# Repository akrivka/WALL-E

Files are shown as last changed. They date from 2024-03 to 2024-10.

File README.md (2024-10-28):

# WALL-E

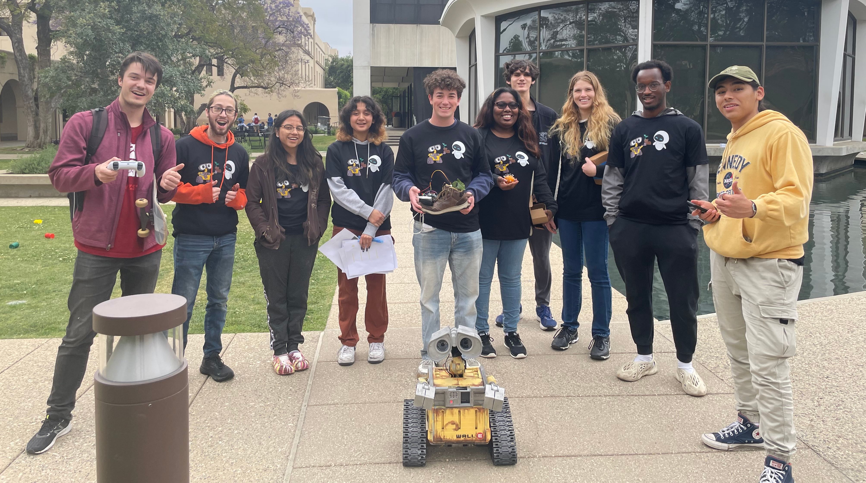
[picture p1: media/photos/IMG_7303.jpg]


For Blacker Hovse Ditch Day 2024 (Caltech tradition), we built a ~70% "real-life" size WALL-E robot, that could be **driven remotely with a PS5 controller, move his head and arms, record and transmit a video feed, speak (faintly)**, and he even had a small storage space in his body (for trash of course!).

Here's my video of him when he was at his best (he's currently sitting in a closet in Blacker to be used as a static showcase project, while I study over in Switzerland...): 

https://github.com/user-attachments/assets/6cdb80cf-8617-4d74-ad6d-1ea3f1ae313b

The model we used was https://www.thingiverse.com/thing:3703555, but we scaled it up by 5/3 which introduced a bunch of challenges. 

**! This repository was used for code-sharing and does not aim to make this project repeatable. Maybe in the future...**

## (rough) List of parts

* Rapsberry Pi 4 (Bluetooth) on Ubuntu 22.04 with ROS2 Humble installed
* PS5 controller
* [RoboClaw 2x15A Motor controller](https://www.basicmicro.com/RoboClaw-2x15A-Motor-Controller_p_10.html)
* [5202 Yellow Jacket Planetary Gear Motor](https://www.gobilda.com/5202-series-yellow-jacket-planetary-gear-motor-26-9-1-ratio-24mm-length-6mm-d-shaft-223-rpm-36mm-gearbox-3-3-5v-encoder/)
* [TowerPro MG996R servos](https://towerpro.com.tw/product/mg996r/)
* [HiLetgo PCA9685 PWM Servo Motor Driver](http://www.hiletgo.com/ProductDetail/2152091.html)
* [Small USB speaker](https://www.amazon.com/shuley-Computer-Speaker-Portable-Sound-bar/dp/B09S3G99HS/ref=sr_1_1)
* some random webcam we found
* 1x 11.1V Zeee LiPo battery (for motor), 1x 7.4V Zee LiPo battery (for servos), some random powerbank (for RPi)

## Some more photos

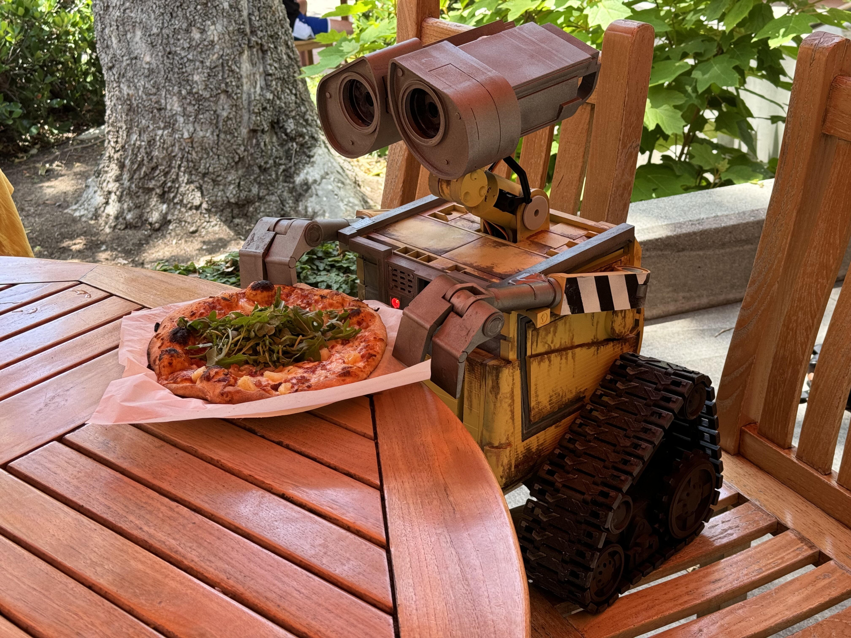
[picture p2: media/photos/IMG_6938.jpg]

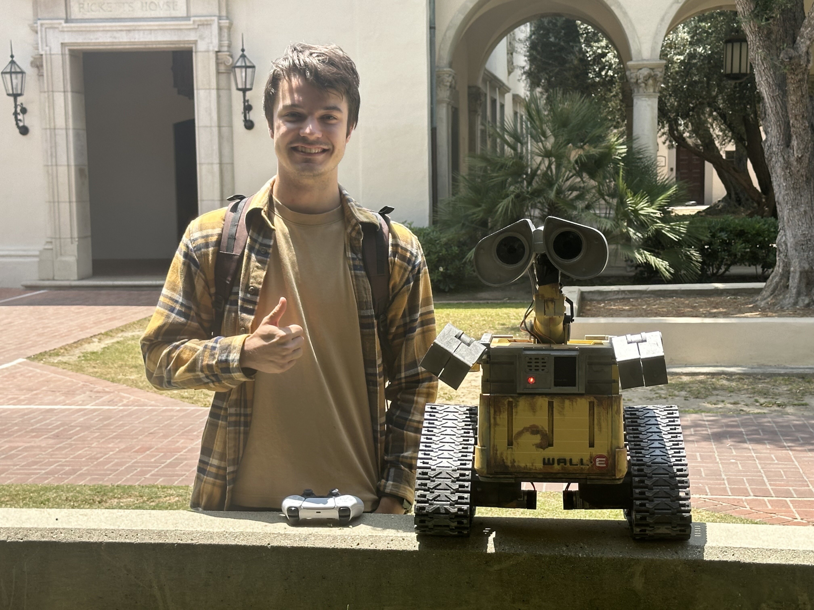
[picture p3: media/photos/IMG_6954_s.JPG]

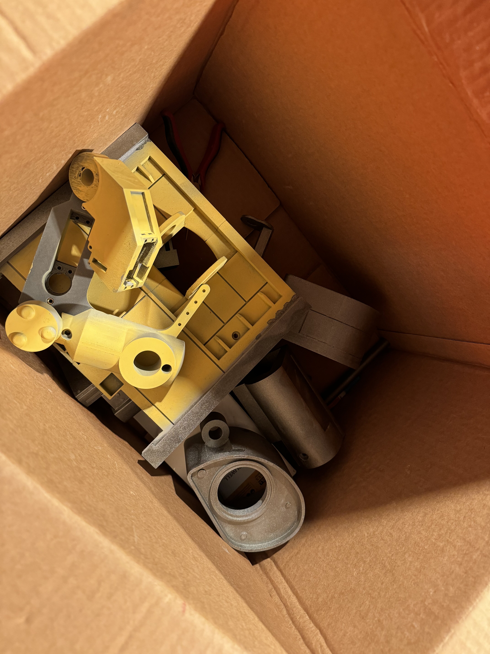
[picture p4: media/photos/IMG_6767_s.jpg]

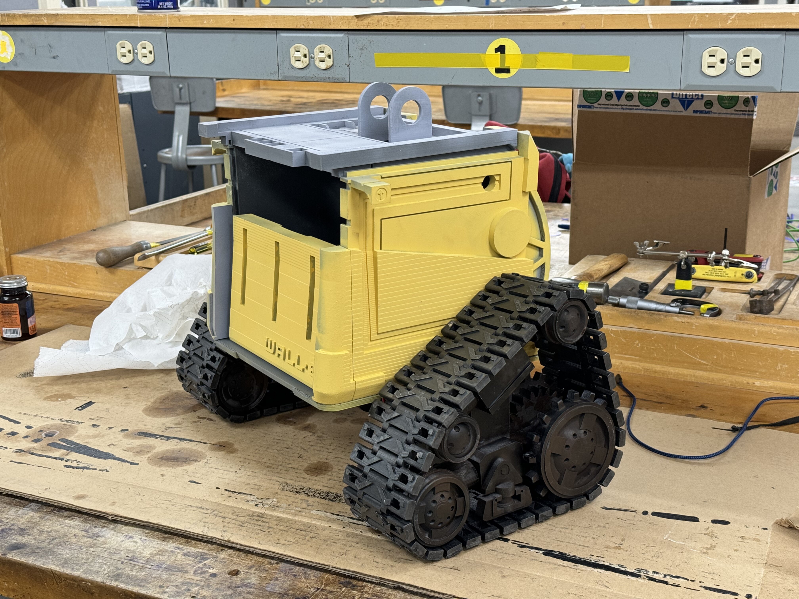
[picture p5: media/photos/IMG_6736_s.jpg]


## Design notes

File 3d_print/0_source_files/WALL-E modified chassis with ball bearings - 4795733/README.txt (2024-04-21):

WALL-E modified chassis with ball bearings by Fendermann on Thingiverse: https://www.thingiverse.com/thing:4795733

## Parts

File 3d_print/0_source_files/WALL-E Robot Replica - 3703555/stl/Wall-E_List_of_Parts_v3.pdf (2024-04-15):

3D Printed WALL-E | List of Parts
# | Name | Quantity Supports Notes

| 3D Printed Components
1 2 3 4 5 6 7 8 9 | Body body-bottom body-back body-front body-front-door body-front-pins-x2 body-left body-right body-top body-neck-servo-holder | 1 1 1 1 2 1 1 1 1 | No Yes Yes Yes No Yes Yes Yes No
10 11 12 13 14 15 16 17 18 19 20 21 22 | Arms arm-servo-bracket-left arm-servo-bracket-right arm-hinge-inner-x2 arm-hinge-outer-x2 arm-hinge-axle-x2 arm-barrel-x2 arm-barrel-end-x2 arm-piston-x2 hand-bracket-x2 hand-axle-x2 hand-finger-left-x2 hand-finger-right-x2 hand-finger-middle-x2 | 1 1 2 2 2 2 2 2 2 2 2 2 2 | No No Yes Yes No Yes No Yes Yes No No No Yes
23 24 25 26 27 28 29 30 31 | Head head-center head-axle eye-back-left eye-back-right eye-middle-left eye-middle-right eye-front-left eye-front-right eye-camera-replica | 1 1 1 1 1 1 1 1 2 | Yes No Yes Yes Yes Yes Yes Yes Yes
32 | eye-camera-mount | 0 | No | < Use this if you want
| | | | to add your own camera
| Neck
33 | neck-bottom-axle | 1 | No
34 | neck-bottom-left | 1 | Yes
35 | neck-bottom-linkage | 1 | No
36 | neck-bottom-right | 1 | Yes
37 | neck-middle-axle | 1 | No
38 | neck-top | 1 | Yes
39 | neck-round-bottom | 1 | No

40 | neck-round-top-left | 1 | Yes
41 | neck-round-top-right | 1 | Yes
42 | neck-wire-guide-left | 1 | No
43 | neck-wire-guide-right | 1 | No
44 | neck-top-linkage | 1 | No
| Wheels
45 | wheel-back-x4 | 4 | No
46 | wheel-front-x4 | 4 | No
47 | wheel-top-x8 | 8 | No
48 | wheel-top-larger-x0 | 0 | No | < Use this instead of
49 | wheel-gear-driven-x2 | 2 | No | wheel-top if you need
50 | wheel-gear-motor-x2 | 2 | No | to increase the tension
51 | wheel-axle-notched-x6 | 6 | No | of the treads.
52 | wheel-axle-back-x2 | 2 | No
53 | wheel-axle-spacer-x8 | 8 | No
54 | wheel-frame-left | 1 | No
55 | wheel-frame-right | 1 | No
56 | wheel-frame-addon-x2 | 2 | No
57 | wheel-bracket-inner-left | 1 | Yes
58 | wheel-bracket-inner-right | 1 | Yes
59 | wheel-bracket-outer-left | 1 | Yes
60 | wheel-bracket-outer-right | 1 | Yes
61 62 | Tanks Treads tread-plate-x70 tread-pin-x140 | 70 140 | No No
Total | | 310

Hardware
h1 linkage bar (paper clip) | 2
h2 M3 Bolt - 10mm length | 14
h3 M3 Bolt - 20mm length | 12
h4 M3 Bolt - 6mm length | 2
h5 M3 Nut | 26

Electronics
e1 Micro Servo Motor | 7
e2 12v Geared DC Motor ⌀37mm | 2
e3 Arduino Uno (or equivalent) | 1
e4 Arduino Motor Shield | 1
e5 12-bit PWM servo driver | 1
e6 12v Battery Pack | 1
e7 12V to 5V Buck Converter | 1
e8 Raspberry Pi | 1 | Optional
e9 USB Camera | 1
e10 Small Speaker | 1

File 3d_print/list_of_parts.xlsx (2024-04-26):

Robot – List of parts
# | Name | Quantity | Supports | Printed? | Notes
 | Body
1 | body-bottom | 1 | No
2 | body-back | 1 | Yes
3 | body-front | 1 | Yes
4 | body-front-door | 1 | Yes
5 | body-front-pins-x2 | 2 | No
6 | body-left | 1 | Yes
7 | body-right | 1 | Yes
8 | body-top | 1 | Yes
9 | body-neck-servo-holder | 1 | No
 | Arms
10 | arm-servo-bracket-left | 1 | No
11 | arm-servo-bracket-right | 1 | No
12 | arm-hinge-inner-x2 | 2 | Yes
13 | arm-hinge-outer-x2 | 2 | Yes
14 | arm-hinge-axle-x2 | 2 | No
15 | arm-barrel-x2 | 2 | Yes
16 | arm-barrel-end-x2 | 2 | No
17 | arm-piston-x2 | 2 | Yes
18 | hand-bracket-x2 | 2 | Yes
19 | hand-axle-x2 | 2 | No
20 | hand-finger-left-x2 | 2 | No
21 | hand-finger-right-x2 | 2 | No
22 | hand-finger-middle-x2 | 2 | Yes
 | Head
23 | head-center | 1 | Yes | x
24 | head-axle | 1 | No | x
25 | eye-back-left | 1 | Yes | x
26 | eye-back-right | 1 | Yes | x
27 | eye-middle-left | 1 | Yes | x | Mirror of eye-middle-right
28 | eye-middle-right | 1 | Yes | x | Altered to fit MG996R servo
29 | eye-front-left | 1 | Yes | x
30 | eye-front-right | 1 | Yes | x
31 | eye-camera-replica | 2 | Yes
32 | eye-camera-mount | 0 | No
 | Neck
33 | neck-bottom-axle | 1 | No
34 | neck-bottom-left | 1 | Yes
35 | neck-bottom-linkage | 1 | No
36 | neck-bottom-right | 1 | Yes
37 | neck-middle-axle | 1 | No
38 | neck-top | 1 | Yes
39 | neck-round-bottom | 1 | No
40 | neck-round-top-left | 1 | Yes
41 | neck-round-top-right | 1 | Yes
42 | neck-wire-guide-left | 1 | No
43 | neck-wire-guide-right | 1 | No
44 | neck-top-linkage | 1 | No
 | Wheels
45 | wheel-back-x4 | 4 | No
46 | wheel-front-x4 | 4 | No
47 | wheel-top-x8 | 8 | No
48 | wheel-top-larger-x0 | 0 | No
49 | wheel-gear-driven-x2 | 2 | No
50 | wheel-gear-motor-x2 | 2 | No
51 | wheel-axle-notched-x6 | 6 | No
52 | wheel-axle-back-x2 | 2 | No
53 | wheel-axle-spacer-x8 | 8 | No
54 | wheel-frame-left | 1 | No
55 | wheel-frame-right | 1 | No
56 | wheel-frame-addon-x2 | 2 | No
57 | wheel-bracket-inner-left | 1 | Yes
58 | wheel-bracket-inner-right | 1 | Yes
59 | wheel-bracket-outer-left | 1 | Yes
60 | wheel-bracket-outer-right | 1 | Yes
 | Tank Treads
61 | tread-plate-x70 | 70 | No
62 | tread-pin-x140 | 140 | No

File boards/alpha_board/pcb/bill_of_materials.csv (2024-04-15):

Id | Designator | Footprint | Quantity | Designation | Supplier and ref
1 | AE1 | EE110_Antenna | 1 | Antenna_Chip
2 | U8 | SOIC-14_3.9x8.7mm_P1.27mm | 1 | LM2902
3 | C17,C18 | C_0805_2012Metric_Pad1.18x1.45mm_HandSolder | 2 | 4pF
4 | R10,R12,R14 | R_0603_1608Metric_Pad0.98x0.95mm_HandSolder | 3 | 24K
5 | R15,R13,R11 | R_0603_1608Metric_Pad0.98x0.95mm_HandSolder | 3 | 36K
6 | D10,D11 | D_1206_3216Metric_Pad1.42x1.75mm_HandSolder | 2 | D_Small_Filled
7 | C1,C3,C2 | CP_EIA-1608-08_AVX-J_Pad1.25x1.05mm_HandSolder | 3 | 10uF
8 | C28 | C_0603_1608Metric_Pad1.08x0.95mm_HandSolder | 1 | 10nF
9 | C12,C21,C16,C14 | CP_EIA-1608-08_AVX-J_Pad1.25x1.05mm_HandSolder | 4 | 4.7uF
10 | ,, |  | 3
11 | C23,C26 | C_0603_1608Metric_Pad1.08x0.95mm_HandSolder | 2 | 10uF
12 | U9 | QFN-24-1EP_3x3mm_P0.4mm_EP1.75x1.6mm | 1 | MPU-9250
13 | U6 | SOIC-20W_7.5x15.4mm_P1.27mm | 1 | 74LVC245
14 | D7,D6,D4,D2,D5,D13,D12,D3 | D_0603_1608Metric_Pad1.05x0.95mm_HandSolder | 8 | D_Small_Filled
15 | C19 | C_0805_2012Metric_Pad1.18x1.45mm_HandSolder | 1 | 1pF
16 | LS1 | SPKR_CVS-1508 | 1 | Speaker
17 | C30,C27,C32,C29,C31 | C_0603_1608Metric_Pad1.08x0.95mm_HandSolder | 5 | 0.1uF
18 | D1 | LED_D3.0mm | 1 | LED
19 | C9,C7 | CP_EIA-1608-08_AVX-J_Pad1.25x1.05mm_HandSolder | 2 | 22uF
20 | J3 | 4x4_Keypad | 1 | ~
21 | C15 | C_0805_2012Metric_Pad1.18x1.45mm_HandSolder | 1 | 1.8pF
22 | RV2 | Potentiometer_Bourns_3296P_Horizontal | 1 | 1k
23 | C4,C11,C8,C5,C10,C6 | CP_EIA-1608-08_AVX-J_Pad1.25x1.05mm_HandSolder | 6 | 100nF
24 | J2 | CON10_2X5_DUK_FTSH_SAI | 1 | JTAG
25 | X1 | Crystal_SMD_2016-4Pin_2.0x1.6mm | 1 | 48MHz
26 | R8,R4,R7 | R_0603_1608Metric_Pad0.98x0.95mm_HandSolder | 3 | 200
27 | L5,L3 | L_0805_2012Metric_Pad1.15x1.40mm_HandSolder | 2 | 3.3nH
28 | L2 | L_0603_1608Metric_Pad1.05x0.95mm_HandSolder | 1 | 6.8uH
29 | RV3,RV1 | Potentiometer_Bourns_3296P_Horizontal | 2 | 10k
30 | J6 | JST_XH_S4B-XH-A-1_1x04_P2.50mm_Horizontal | 1 | SERVO2
31 | L4 | L_0805_2012Metric_Pad1.15x1.40mm_HandSolder | 1 | 2nH
32 | U2,U1 | TO-263-3_TabPin2 | 2 | LM1086
33 | SW2 | SW_SPST_TL3342 | 1 | TEST_BUTTON
34 | C24 | C_0603_1608Metric_Pad1.08x0.95mm_HandSolder | 1 | 250uF
35 | U7 | DIP-8_W7.62mm | 1 | LM386
36 | TP1 | TestPoint_THTPad_2.0x2.0mm_Drill1.0mm | 1 | DIO22
37 | TP2 | TestPoint_THTPad_2.0x2.0mm_Drill1.0mm | 1 | DIO23
38 | J5 | JST_XH_S4B-XH-A-1_1x04_P2.50mm_Horizontal | 1 | SERVO1
39 | TP3 | TestPoint_THTPad_2.0x2.0mm_Drill1.0mm | 1 | DIO24
40 | R3,R2 | R_0603_1608Metric_Pad0.98x0.95mm_HandSolder | 2 | 121
41 | SW1 | SW_SPST_TL3342 | 1 | RESET
42 | DS1 | WINSTAR-WH1604A | 1 | LCD-20X4B
43 | TP5 | TestPoint_THTPad_2.0x2.0mm_Drill1.0mm | 1 | GND
44 | C25 | C_0603_1608Metric_Pad1.08x0.95mm_HandSolder | 1 | 0.05uF
45 | TP4 | TestPoint_THTPad_2.0x2.0mm_Drill1.0mm | 1 | +3.3V
46 | U4 | RGZ0048A_NV | 1 | CC2652
47 | R6 | R_0603_1608Metric_Pad0.98x0.95mm_HandSolder | 1 | 183
48 | X2 | Crystal_SMD_3215-2Pin_3.2x1.5mm | 1 | 32.768KHz
49 | C22 | C_0603_1608Metric_Pad1.08x0.95mm_HandSolder | 1 | 1uF
50 | U5 | SOIC-16_3.9x9.9mm_P1.27mm | 1 | 74LS138
51 | D8 | LED_0603_1608Metric_Pad1.05x0.95mm_HandSolder | 1 | TEST_GREEN
52 | D9 | LED_0603_1608Metric_Pad1.05x0.95mm_HandSolder | 1 | TEST_BLUE
53 | R1 | R_0603_1608Metric_Pad0.98x0.95mm_HandSolder | 1 | 100
54 | R9 | R_0603_1608Metric_Pad0.98x0.95mm_HandSolder | 1 | 10
55 | C20,C13 | C_0805_2012Metric_Pad1.18x1.45mm_HandSolder | 2 | 1.3pF
56 | J4 | microSD_HC_Hirose_DM3D-SF | 1 | Micro_SD_Card
57 | R5 | R_0603_1608Metric_Pad0.98x0.95mm_HandSolder | 1 | 363
58 | R16 | R_0603_1608Metric_Pad0.98x0.95mm_HandSolder | 1 | 4.7k
59 | J1 | My_Power_Connector | 1 | power
60 | L1 | L_7.3x7.3_H3.5 | 1 | BLM18HE152SN1
61 | U3 | SOT-23-5 | 1 | LM372x
62 | B1 | 1049P_KEY | 1 | 1049P

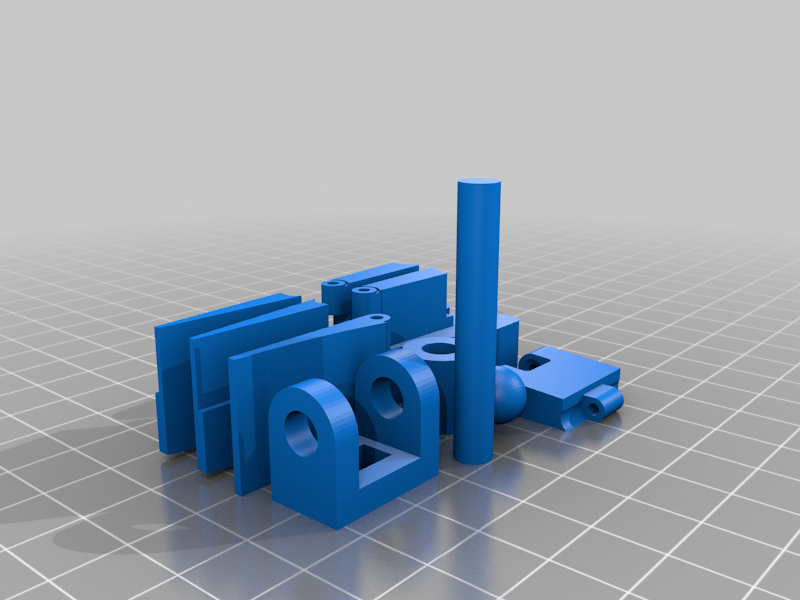
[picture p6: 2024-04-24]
3d_print/0_source_files/Wall-e realistic hand for WALL-E Robot Replica by chillibasket - 5391045/images/Wall-e_hand_parts.png

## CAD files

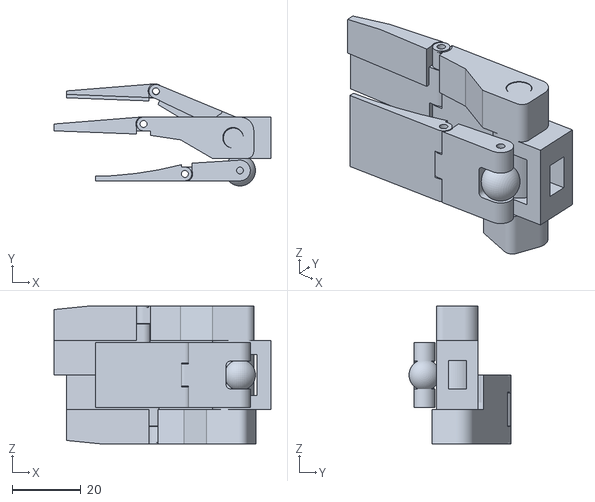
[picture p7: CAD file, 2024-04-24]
3d_print/0_source_files/Wall-e realistic hand for WALL-E Robot Replica by chillibasket - 5391045/files/Wall-e_hand_assembled.stl
63.0 x 29.6 x 40.0

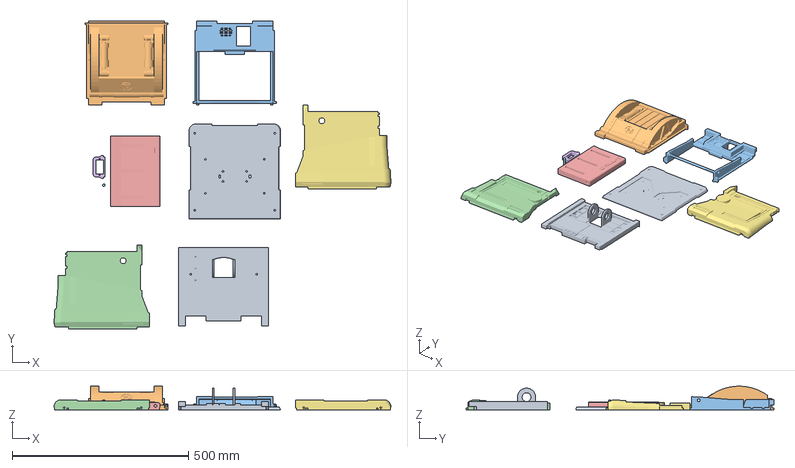
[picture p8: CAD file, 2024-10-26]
3d_print/0.1_source_files/WALL-E Robot Replica - 3703555/stl/body-back.3mf
956.4 x 873.5 x 67.2 mm
body-bottom.stl
body-back.stl
body-front.stl
body-left.stl
body-front-door.stl
body-neck-servo-holder.stl
body-right.stl
body-front-pins-x2.stl
body-top.stl

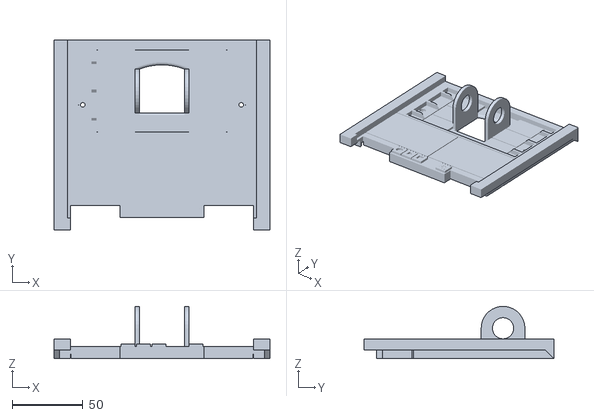
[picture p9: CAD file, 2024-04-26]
3d_print/0_source_files/Accurate Recording Buttons - 5223648/files/New_Wall-e_Top.stl
153.0 x 134.4 x 37.0

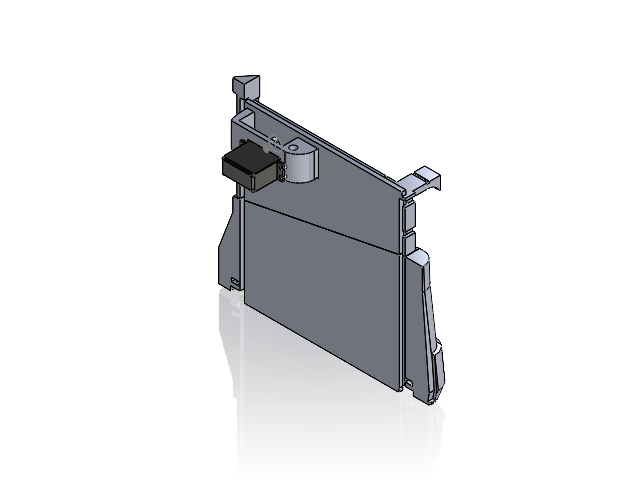
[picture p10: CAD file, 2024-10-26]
3d_print/1_cad/assemblies/body-arm.SLDASM
arm-servo-bracket-left
MG996R
body-left

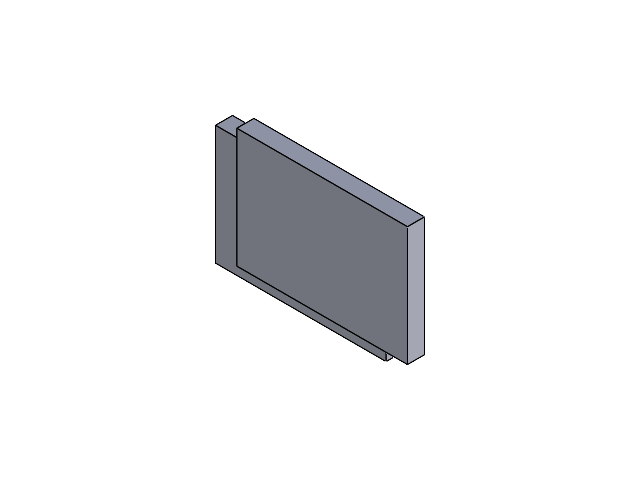
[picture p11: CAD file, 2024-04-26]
boards/alpha_board/enclosure/1_cad/assemblies/alpha_board_enclosure.SLDASM
alpha_board_enclosure_bottom
alpha_board_enclosure_top

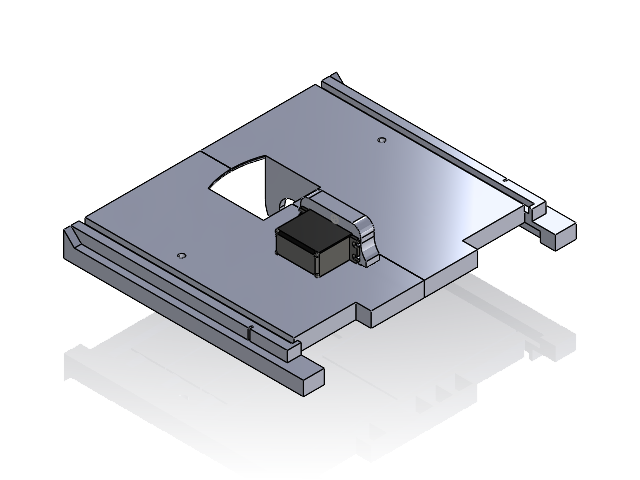
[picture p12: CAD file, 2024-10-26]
3d_print/1_cad/assemblies/body-neck.SLDASM
body-neck-servo-holder
body-top
MG996R

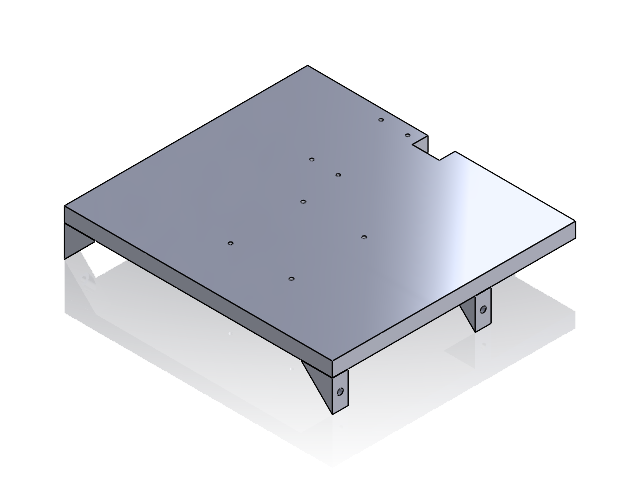
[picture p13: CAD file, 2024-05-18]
3d_print/1_cad/assemblies/body-top-electronics-plate.SLDASM
body-top-electronics-plate
body-top-electronics-bracket x 6

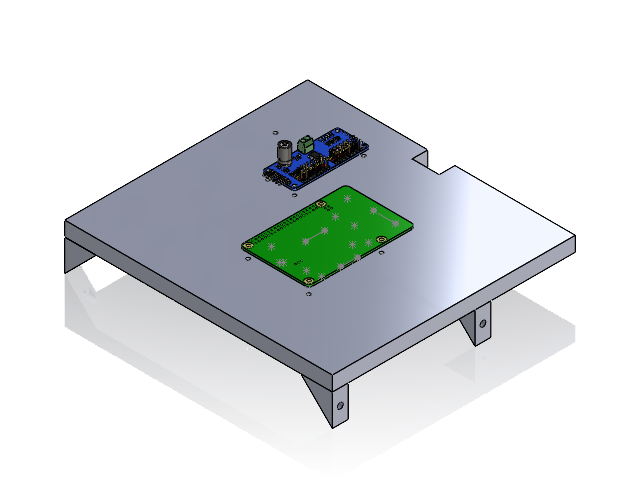
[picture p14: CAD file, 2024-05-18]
3d_print/1_cad/assemblies/body-top-plate-with-stuff.SLDASM
body-top-electronics-plate
body-top-electronics-bracket x 6
PCB, RPi4ModelB
PCA9685 v18

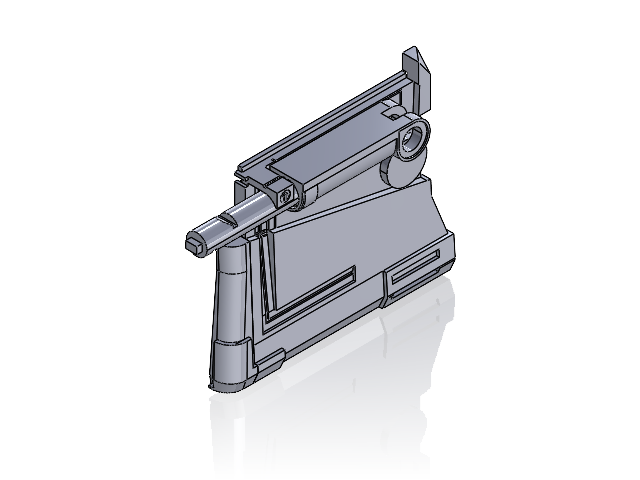
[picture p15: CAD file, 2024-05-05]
3d_print/1_cad/assemblies/Assem1.SLDASM
arm-barrel-x2
arm-piston-x2
body-left

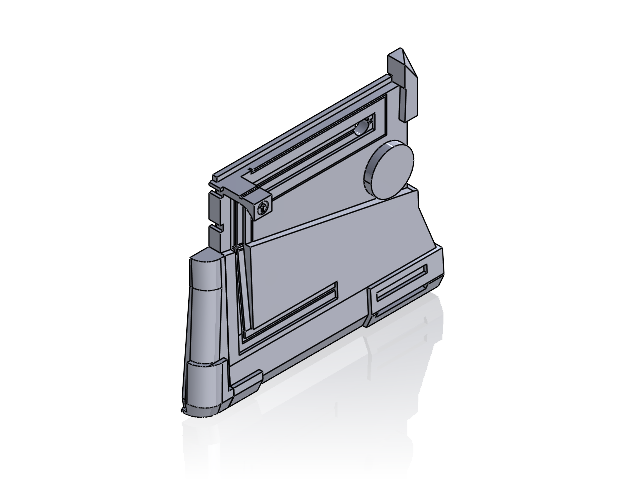
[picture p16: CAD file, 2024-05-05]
3d_print/1_cad/assemblies/body-left.SLDASM
body-left-back
body-left-front

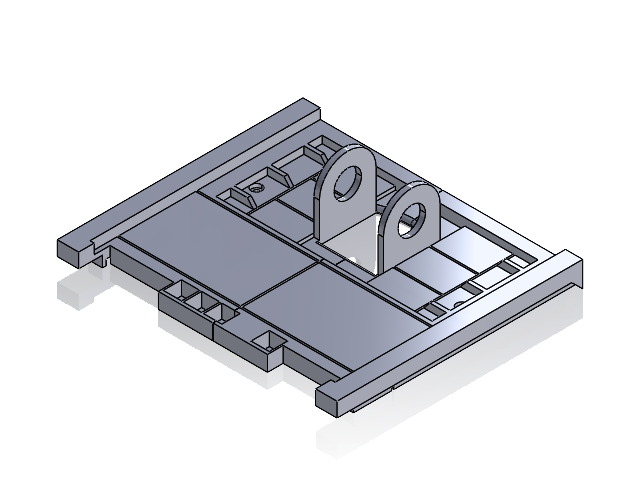
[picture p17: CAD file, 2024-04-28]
3d_print/1_cad/assemblies/body-top-split.SLDASM
body-top-left
body-top-right

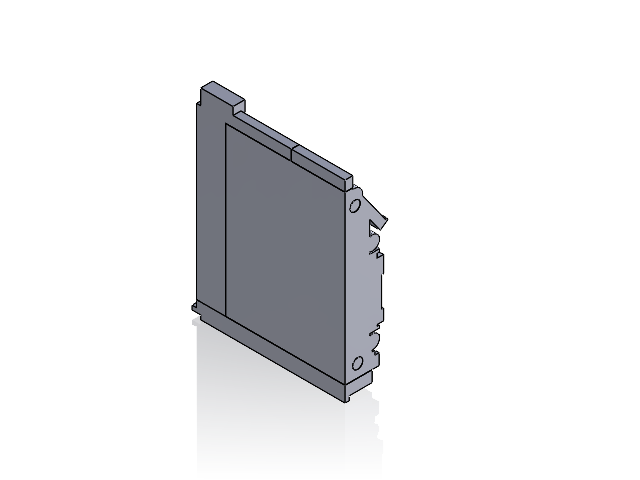
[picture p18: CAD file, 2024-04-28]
3d_print/1_cad/assemblies/body-back-split.SLDASM
body-back-left
body-back-middle
body-back-right

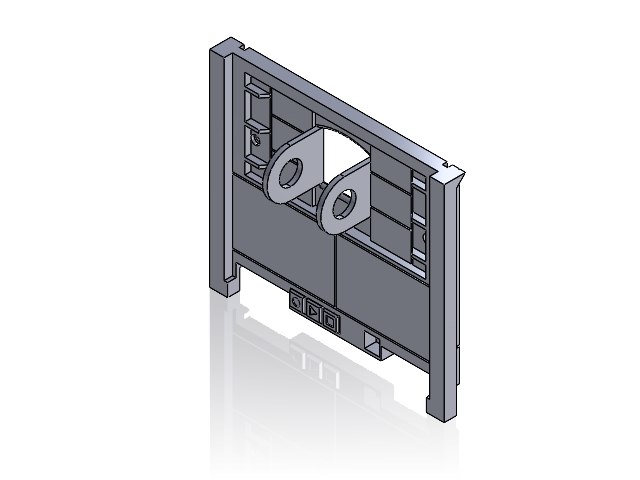
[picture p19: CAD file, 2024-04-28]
3d_print/1_cad/assemblies/body-top.SLDASM
body-top-stop-button
body-top
body-top-play-button
body-top-circle-button

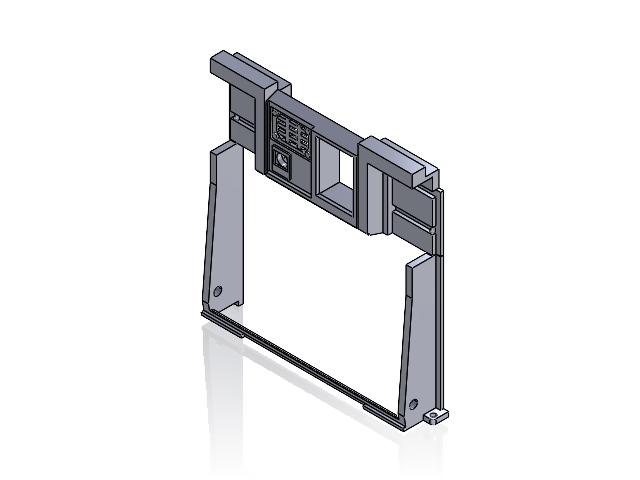
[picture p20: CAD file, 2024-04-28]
3d_print/1_cad/assemblies/body-front-split.SLDASM
body-front-bottom
body-front-top

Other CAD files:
3d_print/1_cad/assemblies/body-left-split.SLDASM
3d_print/1_cad/assemblies/head_neck.SLDASM
3d_print/1_cad/assemblies/arm_hand.SLDASM
3d_print/1_cad/Assem2.SLDASM
3d_print/0_source_files/Pinion gear_motor gear secured with grub screw - 4932959/files/pinion_gear_grub_screw.stl
3d_print/0_source_files/WALL-E (control though Bluetooth Android app via ESP32) - 4816040/files/BracketLock_ESP32_36pin.stl
3d_print/0_source_files/WALL-E (control though Bluetooth Android app via ESP32) - 4816040/files/Bracket_ESP32_36pin.stl
3d_print/0_source_files/WALL-E (control though Bluetooth Android app via ESP32) - 4816040/files/Bracket_ESP32_36pin_v1.stl
3d_print/0_source_files/WALL-E (control though Bluetooth Android app via ESP32) - 4816040/files/Bracket_ESP32_36pin_v2.stl
3d_print/0_source_files/WALL-E (control though Bluetooth Android app via ESP32) - 4816040/files/Bracket_Servo_Module.stl
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

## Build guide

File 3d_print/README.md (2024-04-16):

# Wall-E 3D print files

This is 3D print project based on:

* https://www.thingiverse.com/thing:3703555/remixes (Thingiverse post)
* https://wired.chillibasket.com/3d-printed-wall-e/ (dude's own blogpost with more details).

Our version is 5/3x scaled, which brings up the model to about 70% "life-size". All the electronics will be custom based on boards and components from the class EE 110 at Caltech.

We will be using the MG996R servos instead of SG90 (~2x bigger, much stronger), so need to rework the attachments. We'll also probably using a different DC motor.

It would be nice to implement the following remixes:

1. Track/drive improvements recommended in the blogpost (@Neil / @Jack which to choose?)
2. [Motorised eyebrows](https://www.thingiverse.com/thing:5420196)
3. Servo for door hinge? (need to find if someone has done)

Small parts will be printed on Bambu X1 Carbon printers and large parts on a CraftBot Flow XL printer. All parts will be sand-blasted and spary painted before assembly.

## Folder structure 

The idea of the subfolders is:

- `0.1_source_files`: Files directly downloaded from the internet and other then unzipping and minor folder renaming/mergin, they are unmodified
- `0.2_converted`: Parts converted to SolidWorks .sldprt
- `0.3_scaled`: Parts scaled by 5/3, nothing else is done to them
- `1_sldprt`: Current SolidWorks parts with any changes/additions. A kind of source of truth.
- `2_stl`: .stl export for 3D printing
- `3_batches`: 3D printer specific files (.3mf for Bambu, ...) with groups of parts (importted from 2_stl/) for batch printing, indexed in chronologically order

Furthermore, I am also tracking all parts and components in `list_of_parts.xlsx`.

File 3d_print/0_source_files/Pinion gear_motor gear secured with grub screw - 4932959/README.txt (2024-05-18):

Pinion gear/motor gear secured with grub screw by dmdiego on Thingiverse: https://www.thingiverse.com/thing:4932959

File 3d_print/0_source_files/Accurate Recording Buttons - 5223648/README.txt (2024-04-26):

Accurate Recording Buttons by Xyphinon on Thingiverse: https://www.thingiverse.com/thing:5223648

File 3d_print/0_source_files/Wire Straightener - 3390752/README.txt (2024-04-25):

Wire Straightener by Regorlas on Thingiverse: https://www.thingiverse.com/thing:3390752

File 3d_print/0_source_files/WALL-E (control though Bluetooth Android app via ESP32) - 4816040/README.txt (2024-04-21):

WALL-E (control though Bluetooth Android app via ESP32) by ZDC on Thingiverse: https://www.thingiverse.com/thing:4816040

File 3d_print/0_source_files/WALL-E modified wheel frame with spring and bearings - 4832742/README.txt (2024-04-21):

WALL-E modified wheel frame with spring and bearings by dmdiego on Thingiverse: https://www.thingiverse.com/thing:4832742

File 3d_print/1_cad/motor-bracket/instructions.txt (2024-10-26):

Hi, thanks for offering to help with this.

I am building a real-life WALL-E according to this:
* https://wired.chillibasket.com/3d-printed-wall-e/
* https://www.thingiverse.com/thing:3703555

I am building it 5/3 scaled up from the original version, 
and I'm using a stronger motor:
https://www.servocity.com/5202-series-yellow-jacket-planetary-gear-motor-26-9-1-ratio-24mm-length-6mm-d-shaft-223-rpm-36mm-gearbox-3-3-5v-encoder/

I need to adjust the motor brackets so that the axle and screw holes 
are still in the same location, but the circular motor bracket fits 
the new motor (it's the same diameter, but it's longer. Because of the
5/3 scaling, it is too small if you scale up the bracket directly.)

In this zip there are the source .step files, which means that the 
brackets are UNSCALED!!! So you need to scale them up by 5/3 if you're
using a different software. There's also a Solidworks part which is scaled
up. I also included the motor .step file and converted to Solidworks part.
If at doubt, confer the links above or message me.

Again: the axle and screw locations should stay the same. Assume I've just 
taken all the models and scaled them up by 5/3 (which is basically what I
did +- some other adjustments).

You can send me this same zip file with the modified parts.

Thanks
Adam Krivka#adamkrivka

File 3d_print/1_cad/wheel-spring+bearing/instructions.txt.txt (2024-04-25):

Notes:
	* Only parts for ball bearing/spring adjustement sare in this zip, namely
	  wheel-gear-motor and wheel-famre-addon and wheel-bracket parts are missing
	* Files not taken from a remix are also available in .step, parts from remixes
	  only in .stl unfortunately
	* Assembly Instructions from original project timestamped at wheel assembly:
		https://youtu.be/ZRK9f4FZlD8?si=3oYJPzSPwdFrIE1S&t=244
	* Parts are taken from remixes:
		wheel-frame-left, wheel-frame-right, wheel-functional-part
		(https://www.thingiverse.com/thing:4832742)
			adds ball bearings (original size 6700 10x15x4mm)
			and spring tread tensioning
			
		wheel-front-x4 (https://www.thingiverse.com/thing:4932310)
			same remix as tread paperclip linkage, 
			it should fit better with it

Steps:

0. IMPORTANT: All parts should be first scaled up by 5/3. 
All files in this zip start original/unscaled.

1. wheel-frame-left, wheel-frame-right, and wheel-functional-part 
need to be adjusted to fit a 6803 bearing, which is 17x26x5mm. They
should be inserted using a press fit, but add 0.2-0.3 to outer diameter
(or use your own judgement). 
Here's the specific ball bearing I ordered:
	https://www.amazon.com/dp/B09D2P5K9Q

2. All remaining parts except should be adjusted such that the axles 
fit into the ball bearing (so should be diatemer 17), and the wheels 
fit onto the axels.

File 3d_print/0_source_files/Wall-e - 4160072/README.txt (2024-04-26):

Wall-e by alvarolg on Thingiverse: https://www.thingiverse.com/thing:4160072

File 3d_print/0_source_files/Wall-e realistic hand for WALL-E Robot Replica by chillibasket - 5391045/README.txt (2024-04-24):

Wall-e realistic hand for "WALL-E Robot Replica" by chillibasket by Wujek_k on Thingiverse: https://www.thingiverse.com/thing:5391045

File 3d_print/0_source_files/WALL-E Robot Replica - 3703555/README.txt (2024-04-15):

WALL-E Robot Replica by chillibasket on Thingiverse: https://www.thingiverse.com/thing:3703555

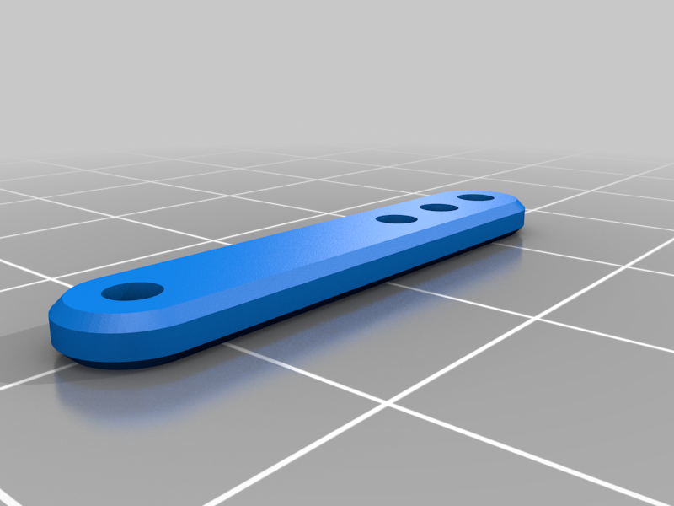
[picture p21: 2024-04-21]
3d_print/0_source_files/WALL-E (control though Bluetooth Android app via ESP32) - 4816040/images/Linkage_MKIII.png

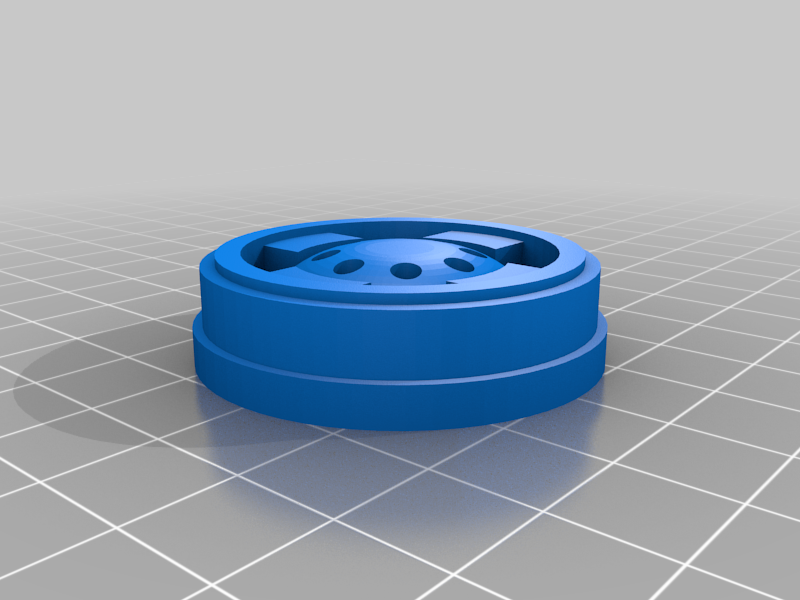
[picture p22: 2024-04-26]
3d_print/0_source_files/Wall-e - 4160072/images/wheel-front-x4.png

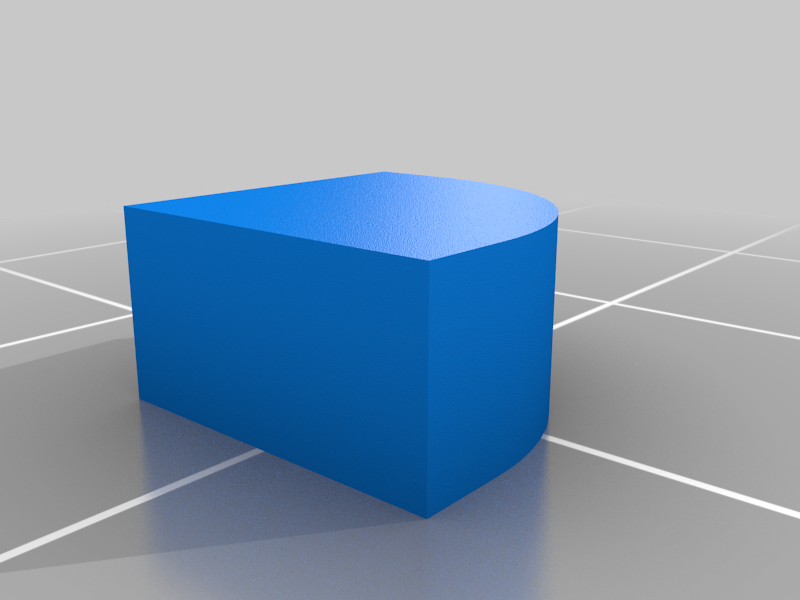
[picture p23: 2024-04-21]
3d_print/0_source_files/WALL-E (control though Bluetooth Android app via ESP32) - 4816040/images/Right-A_Door_Magnet_addon.png

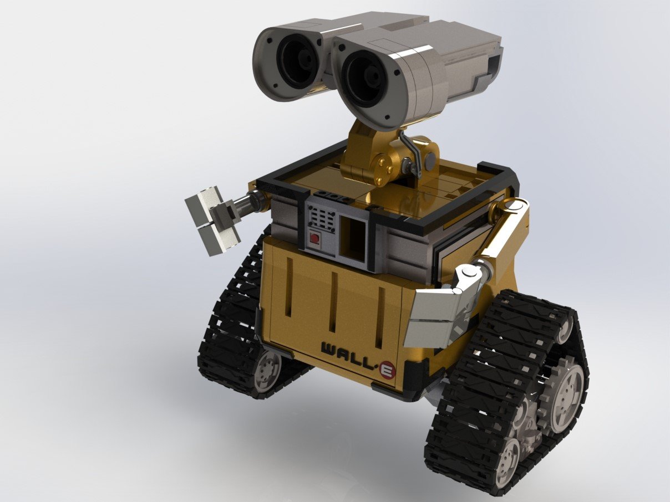
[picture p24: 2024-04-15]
3d_print/0_source_files/WALL-E Robot Replica - 3703555/images/Wall-E_Rendering.JPG

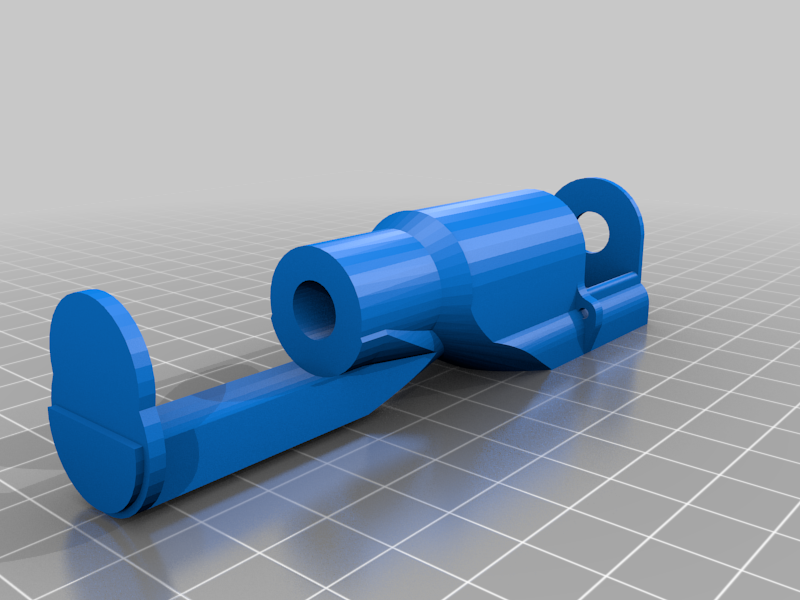
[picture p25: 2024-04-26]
3d_print/0_source_files/Wall-e - 4160072/images/head-center.png

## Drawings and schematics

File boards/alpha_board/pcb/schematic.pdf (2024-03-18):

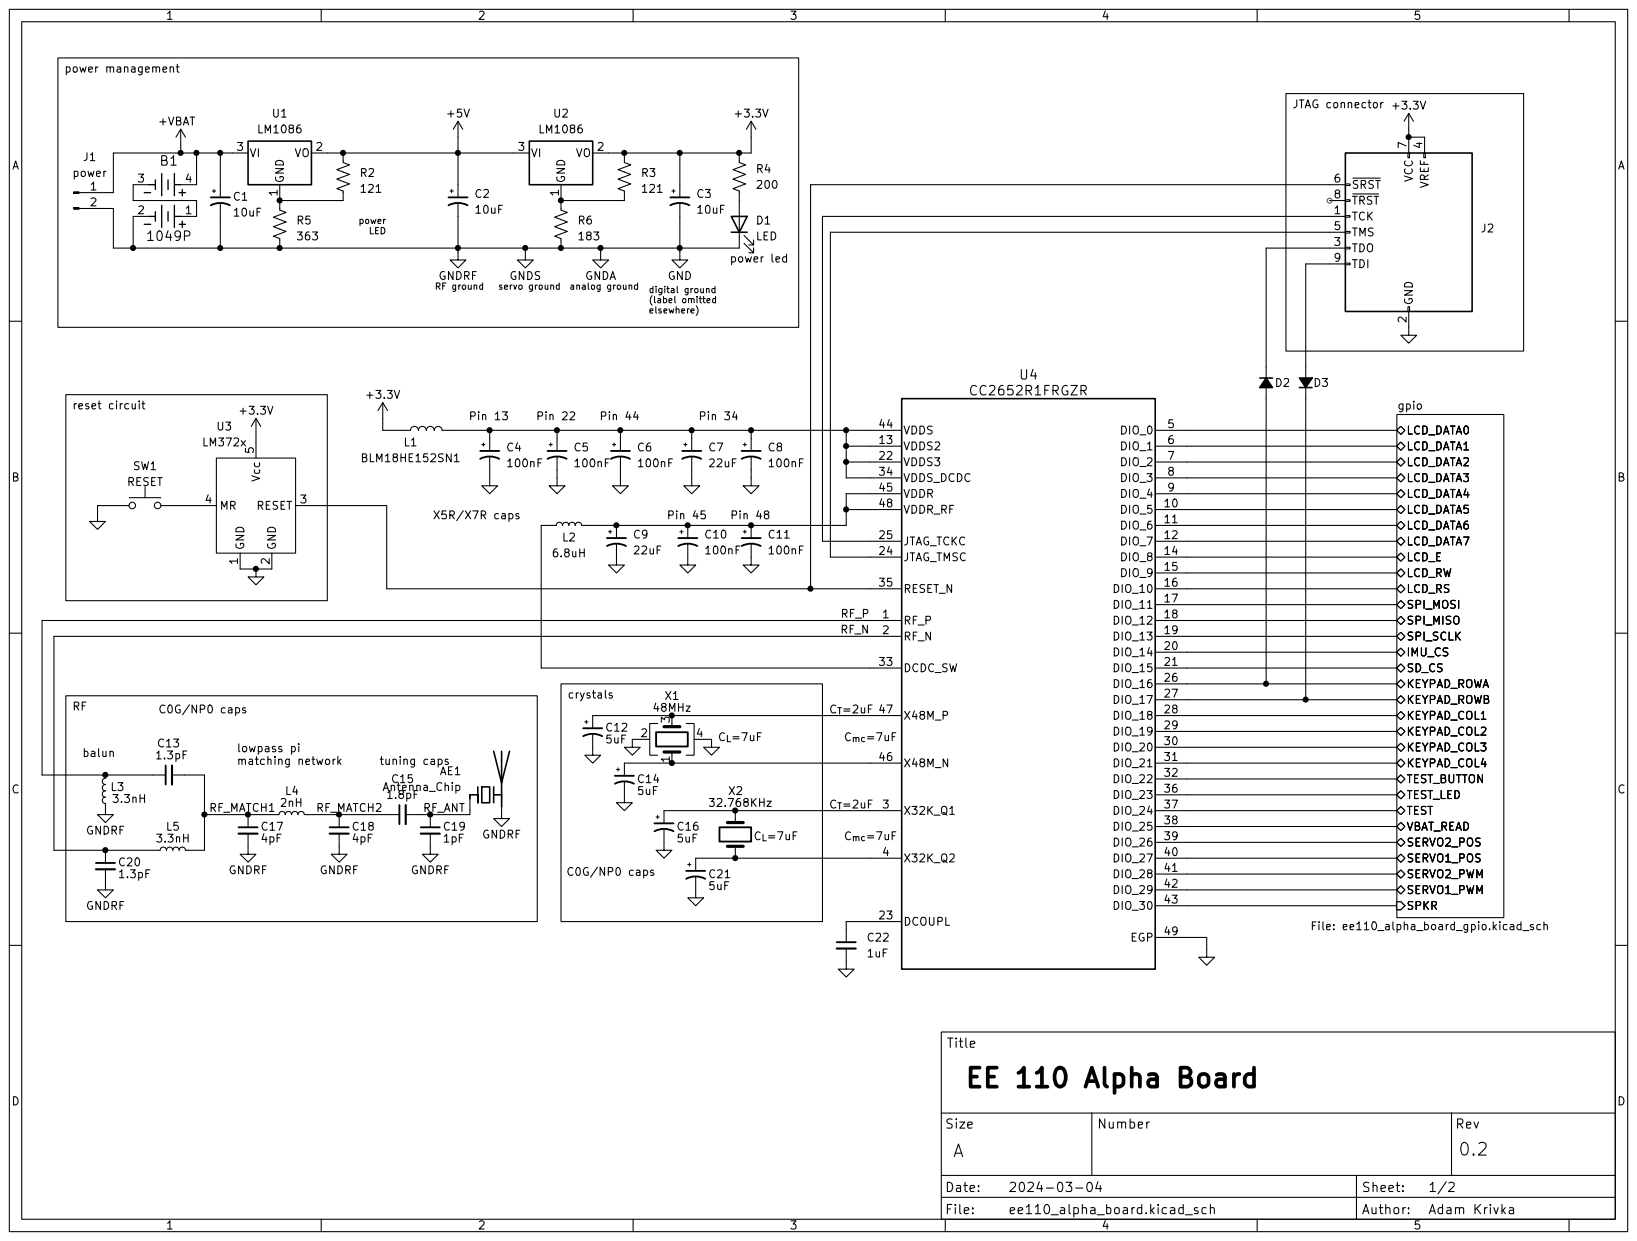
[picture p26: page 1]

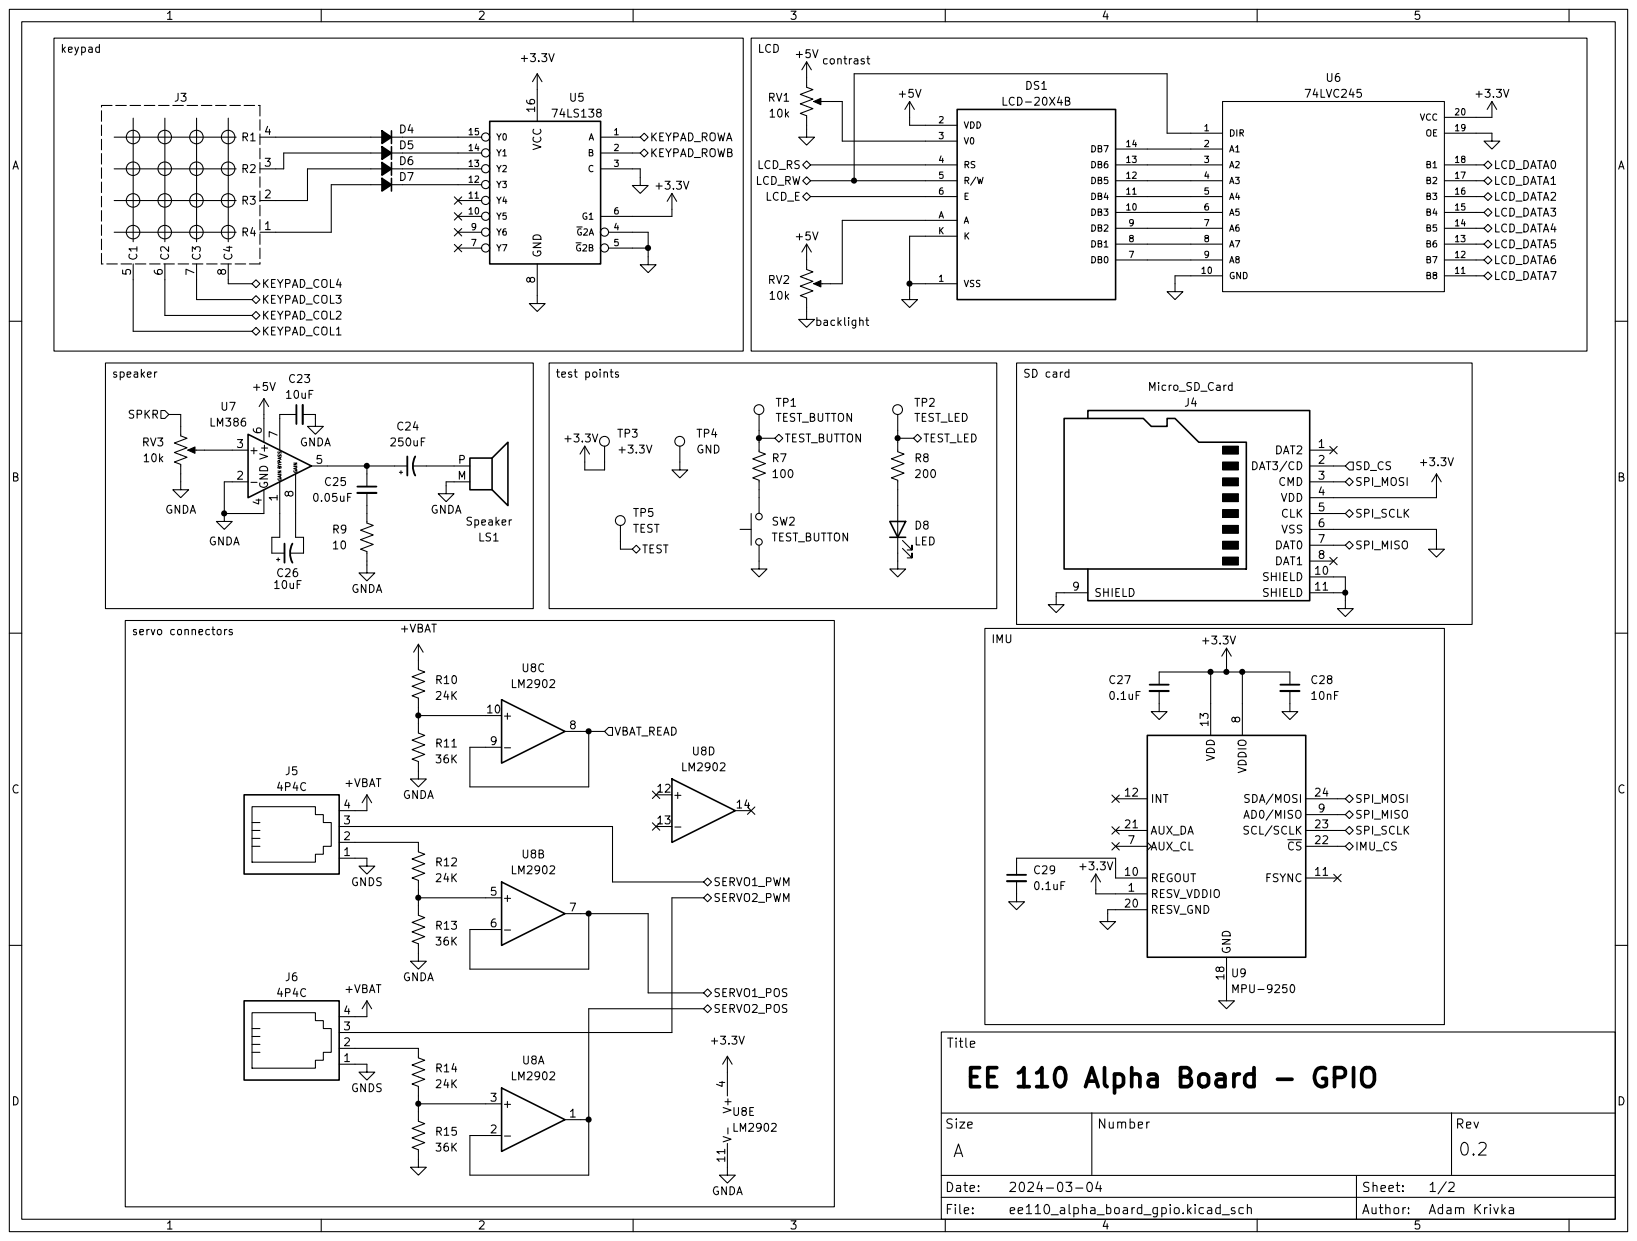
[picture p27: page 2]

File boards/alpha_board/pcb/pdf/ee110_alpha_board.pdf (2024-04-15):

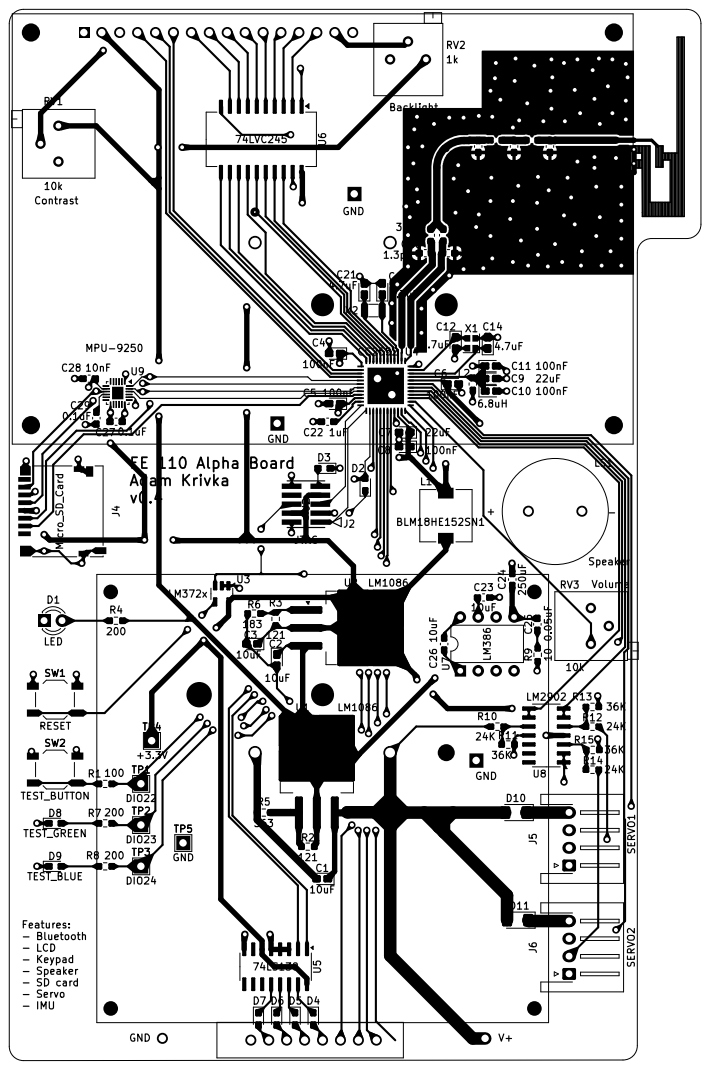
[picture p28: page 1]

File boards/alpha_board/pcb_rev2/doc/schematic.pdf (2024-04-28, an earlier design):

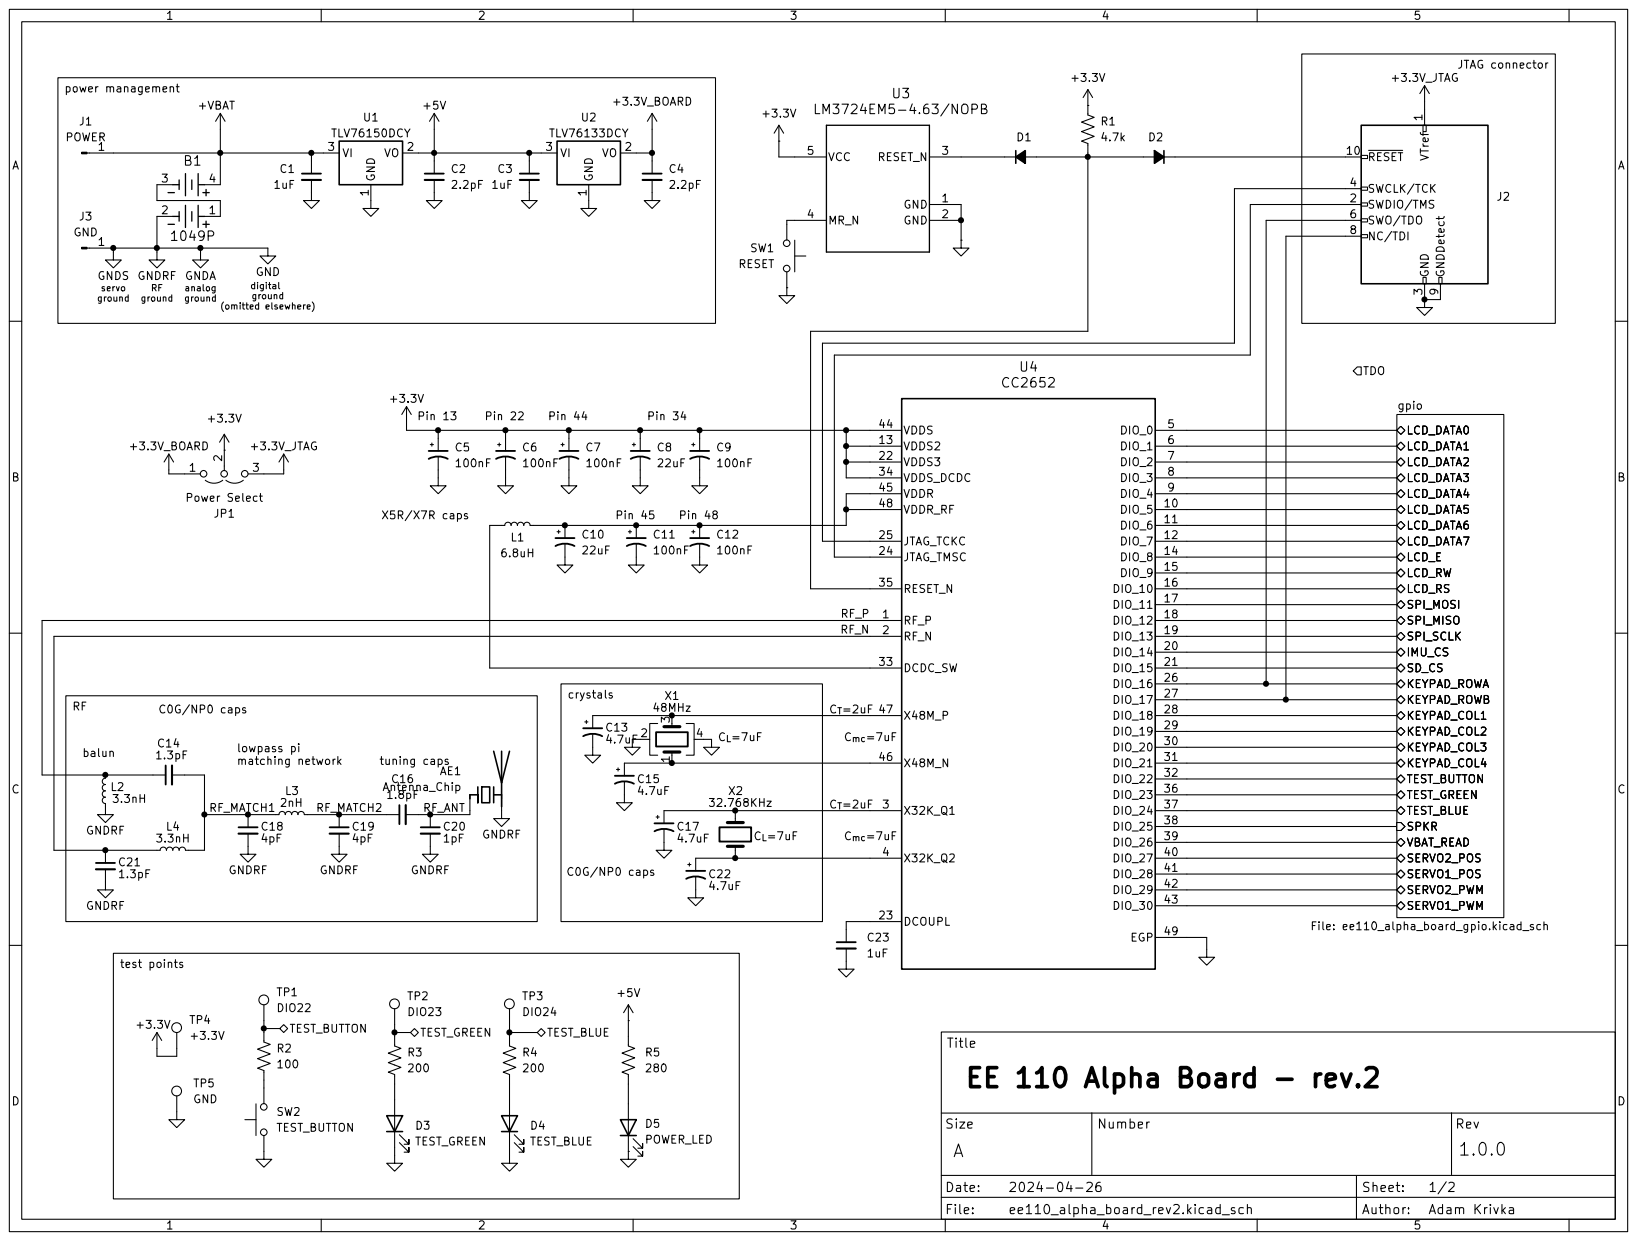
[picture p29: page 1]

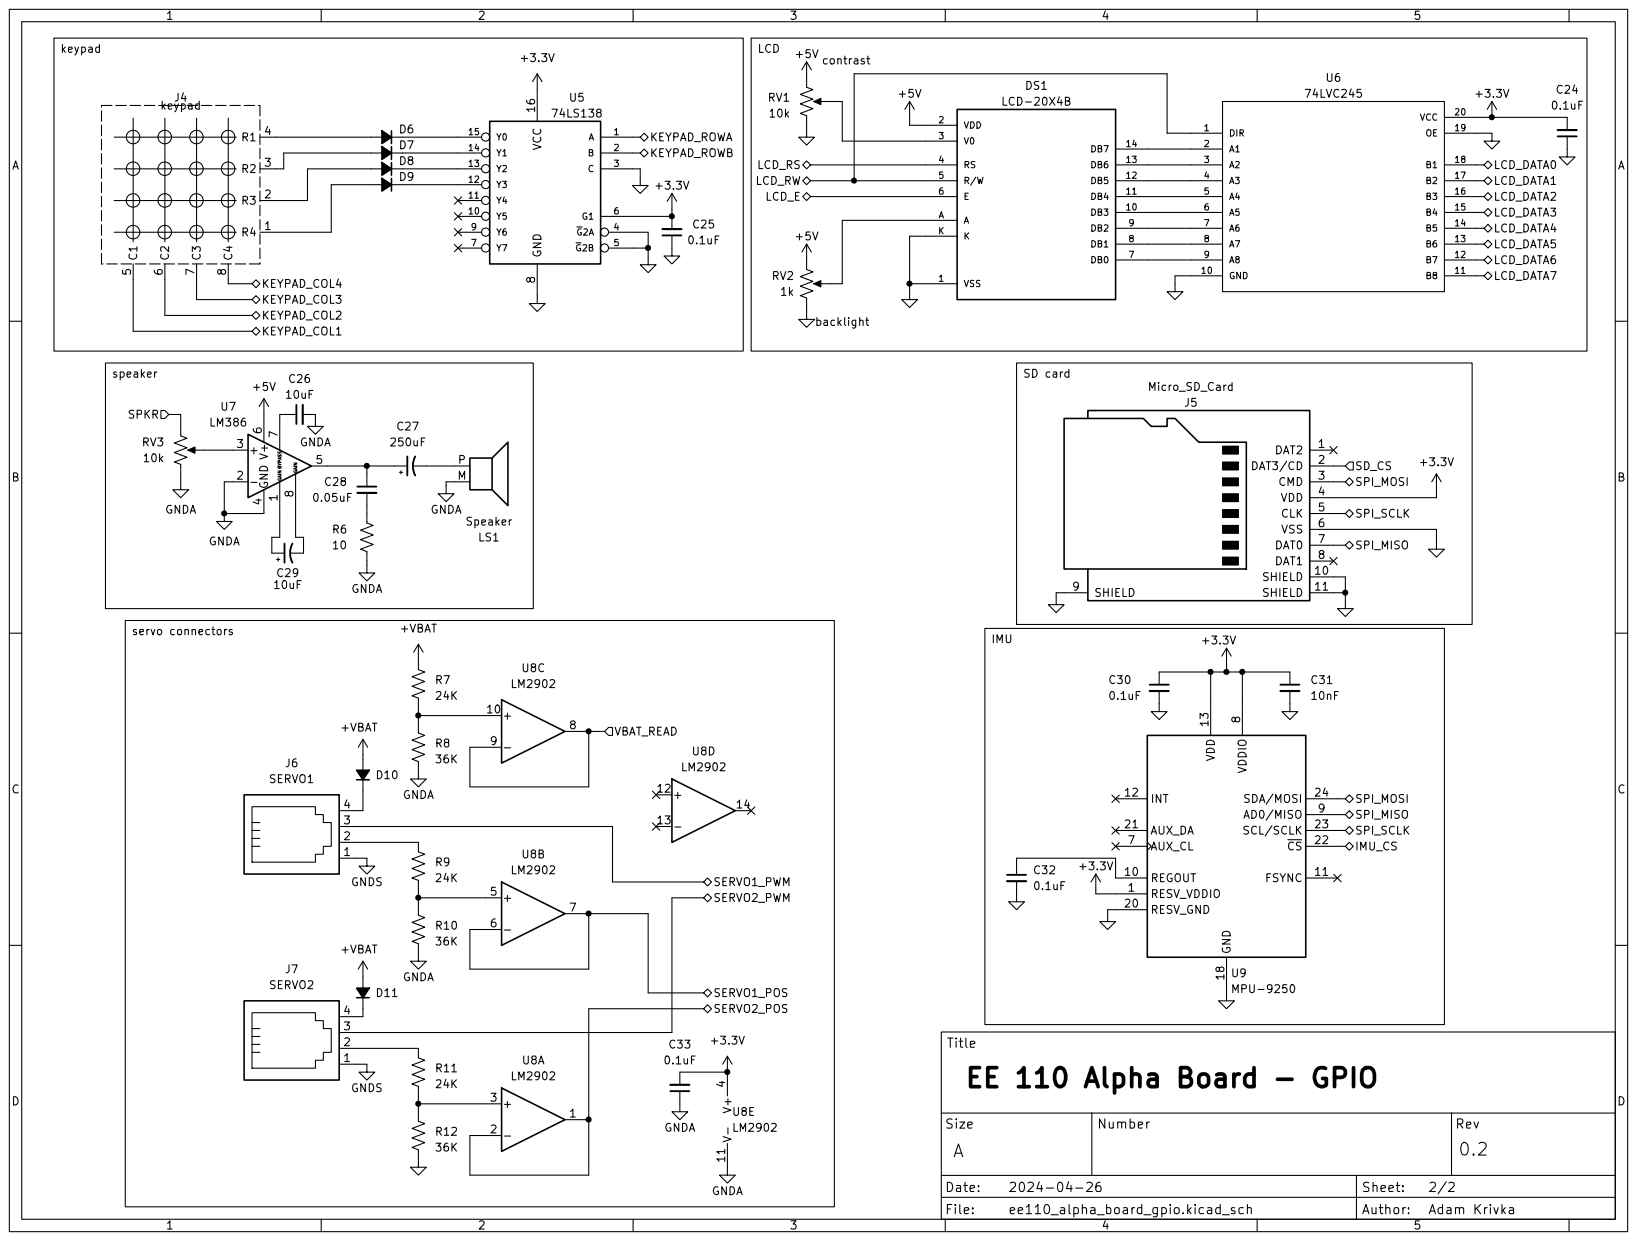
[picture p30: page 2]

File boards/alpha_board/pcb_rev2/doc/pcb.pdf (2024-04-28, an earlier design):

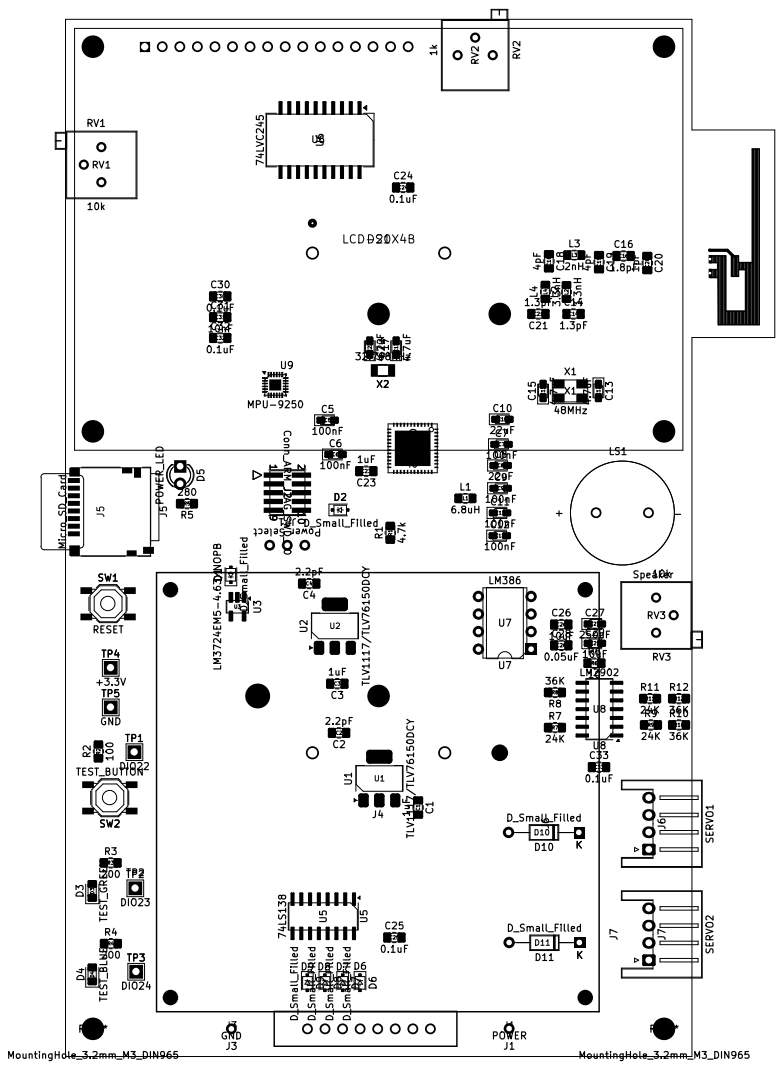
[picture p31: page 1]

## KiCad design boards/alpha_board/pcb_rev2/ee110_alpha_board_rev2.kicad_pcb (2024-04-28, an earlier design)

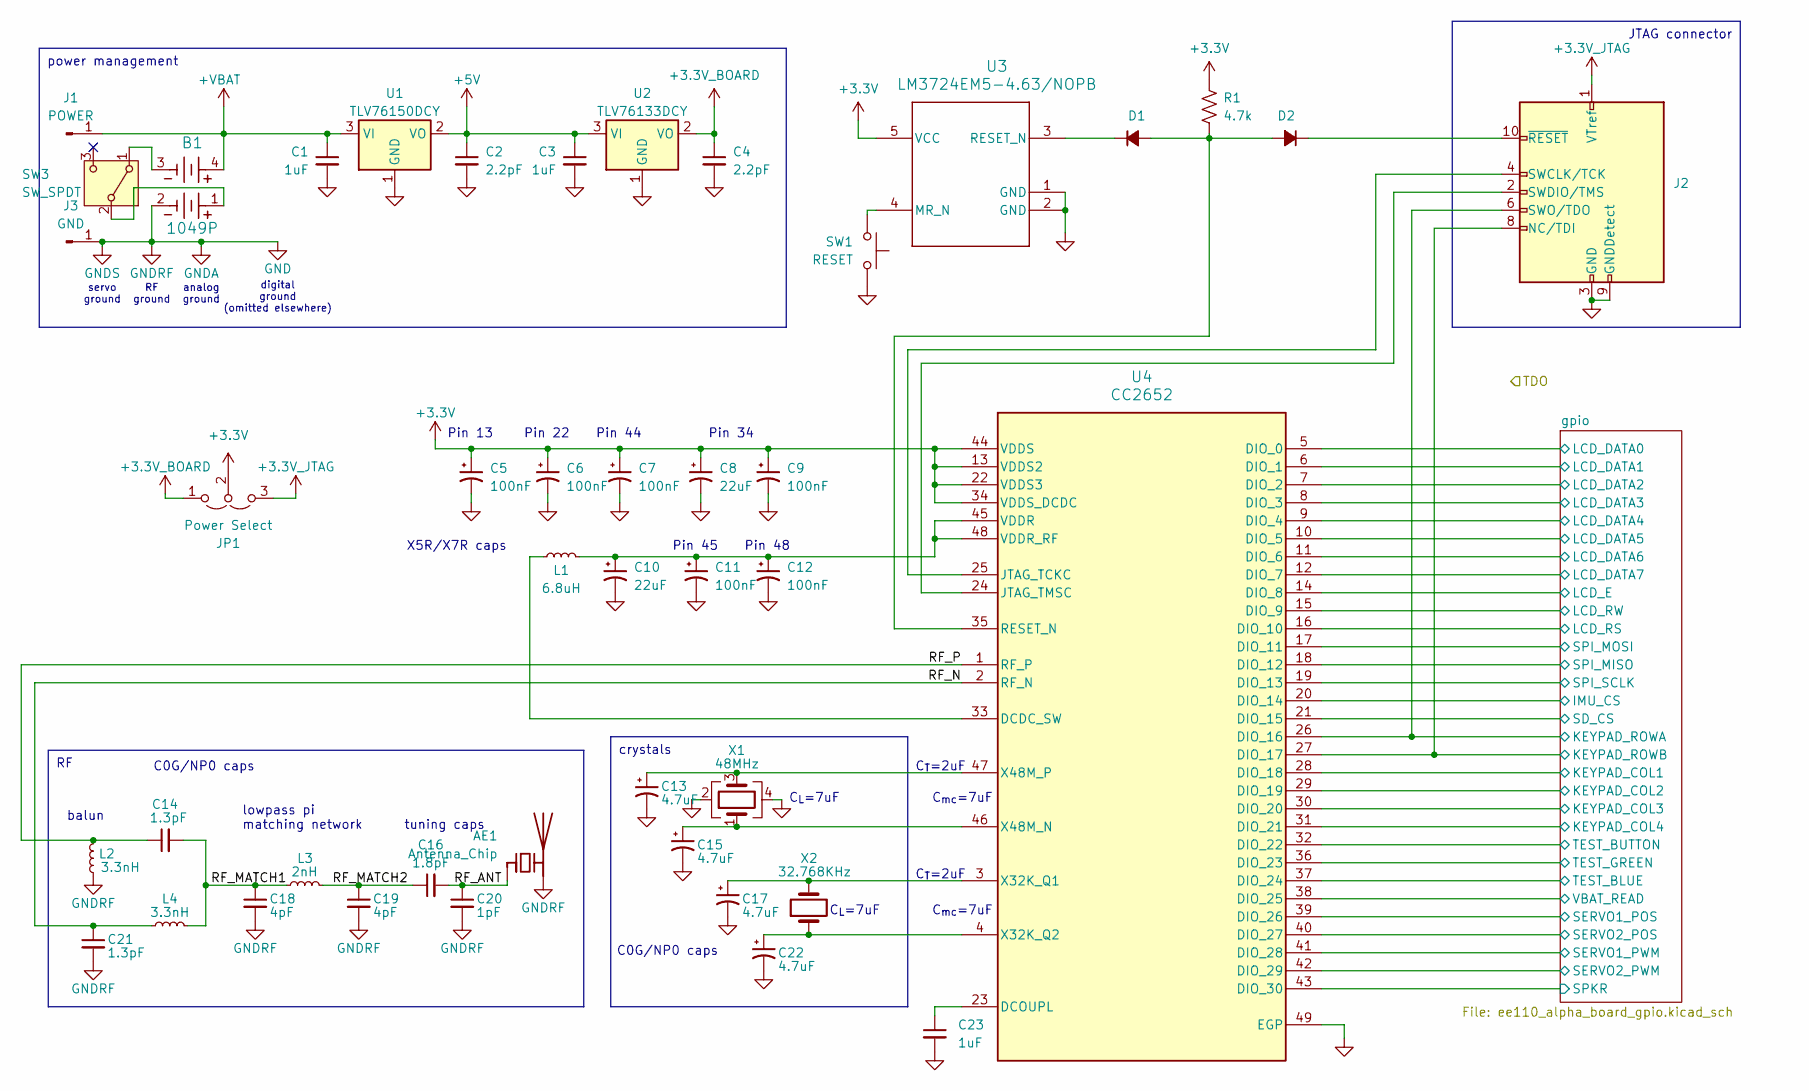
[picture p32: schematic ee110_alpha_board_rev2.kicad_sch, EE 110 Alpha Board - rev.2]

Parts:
AE1: Antenna_Chip; EE110_Antenna
B1: 1049P; 1049P_KEY
C1, C3, C23: 1uF; C_0805_2012Metric_Pad1.18x1.45mm_HandSolder
C2, C4: 2.2pF; C_0805_2012Metric_Pad1.18x1.45mm_HandSolder
C5, C6, C7, C9, C11, C12: 100nF; CP_EIA-2012-12_Kemet-R_Pad1.30x1.05mm_HandSolder
C8, C10: 22uF; CP_EIA-2012-12_Kemet-R_Pad1.30x1.05mm_HandSolder
C13, C15, C17, C22: 4.7uF; CP_EIA-2012-12_Kemet-R_Pad1.30x1.05mm_HandSolder
C14, C21: 1.3pF; C_0805_2012Metric_Pad1.18x1.45mm_HandSolder
C16: 1.8pF; C_0805_2012Metric_Pad1.18x1.45mm_HandSolder
C18, C19: 4pF; C_0805_2012Metric_Pad1.18x1.45mm_HandSolder
C20: 1pF; C_0805_2012Metric_Pad1.18x1.45mm_HandSolder
D1, D2: D_Small_Filled; D_SOD-323F
J1: POWER; 1pin
J2: Conn_ARM_JTAG_SWD_10; CON10_2X5_DUK_FTSH_SAI
J3: GND; 1pin
JP1: Power Select; 3pin_jumper
L1: 6.8uH; L_0805_2012Metric_Pad1.15x1.40mm_HandSolder
L2, L4: 3.3nH; L_0805_2012Metric_Pad1.15x1.40mm_HandSolder
L3: 2nH; L_0805_2012Metric_Pad1.15x1.40mm_HandSolder
R1: 4.7k; R_0805_2012Metric_Pad1.20x1.40mm_HandSolder
SW1: RESET; SW_SPST_TL3342
SW3: SW_SPDT; EG1903
U1: TLV76150DCY; SOT-223-3_TabPin2
U2: TLV76133DCY; SOT-223-3_TabPin2
U3: LM3724EM5-4.63/NOPB; SOT-23-5_HandSoldering
U4: CC2652; RGZ0048A_NV
X1: 48MHz; Crystal_SMD_5032-4Pin_5.0x3.2mm
X2: 32.768KHz; Crystal_SMD_3215-2Pin_3.2x1.5mm

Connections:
+3.3V: C5.1, C6.1, C7.1, C8.1, C9.1, JP1.2 (C), R1.1, U3.5 (VCC), U4.13 (VDDS2), U4.22 (VDDS3), U4.34 (VDDS_DCDC), U4.44 (VDDS); also elsewhere on the board
+3.3V_BOARD: C4.1, JP1.1 (A), U2.2 (VO)
+3.3V_JTAG: J2.1 (VTref), JP1.3 (B)
+5V: C2.1, C3.1, U1.2 (VO), U2.3 (VI); also elsewhere on the board
+VBAT: B1.4, C1.1, J1.1, U1.3 (VI); also elsewhere on the board
/RF_ANT: AE1.1 (FEED), C16.2, C20.1
/RF_MATCH1: C14.2, C18.1, L3.1, L4.2
/RF_MATCH2: C16.1, C19.1, L3.2
/RF_N: C21.1, L4.1, U4.2 (RF_N)
/RF_P: C14.1, L2.2, U4.1 (RF_P)
/gpio/IMU_CS: U4.20 (DIO_14); also elsewhere on the board
/gpio/KEYPAD_COL1: U4.28 (DIO_18); also elsewhere on the board
/gpio/KEYPAD_COL2: U4.29 (DIO_19); also elsewhere on the board
/gpio/KEYPAD_COL3: U4.30 (DIO_20); also elsewhere on the board
/gpio/KEYPAD_COL4: U4.31 (DIO_21); also elsewhere on the board
/gpio/KEYPAD_ROWA: J2.6 (SWO/TDO), U4.26 (DIO_16); also elsewhere on the board
/gpio/KEYPAD_ROWB: J2.8 (NC/TDI), U4.27 (DIO_17); also elsewhere on the board
/gpio/LCD_DATA0: U4.5 (DIO_0); also elsewhere on the board
/gpio/LCD_DATA1: U4.6 (DIO_1); also elsewhere on the board
/gpio/LCD_DATA2: U4.7 (DIO_2); also elsewhere on the board
/gpio/LCD_DATA3: U4.8 (DIO_3); also elsewhere on the board
/gpio/LCD_DATA4: U4.9 (DIO_4); also elsewhere on the board
/gpio/LCD_DATA5: U4.10 (DIO_5); also elsewhere on the board
/gpio/LCD_DATA6: U4.11 (DIO_6); also elsewhere on the board
/gpio/LCD_DATA7: U4.12 (DIO_7); also elsewhere on the board
/gpio/LCD_E: U4.14 (DIO_8); also elsewhere on the board
/gpio/LCD_RS: U4.16 (DIO_10); also elsewhere on the board
/gpio/LCD_RW: U4.15 (DIO_9); also elsewhere on the board
/gpio/SD_CS: U4.21 (DIO_15); also elsewhere on the board
/gpio/SERVO1_POS: U4.39 (DIO_26); also elsewhere on the board
/gpio/SERVO1_PWM: U4.41 (DIO_28); also elsewhere on the board
/gpio/SERVO2_POS: U4.40 (DIO_27); also elsewhere on the board
/gpio/SERVO2_PWM: U4.42 (DIO_29); also elsewhere on the board
/gpio/SPI_MISO: U4.18 (DIO_12); also elsewhere on the board
/gpio/SPI_MOSI: U4.17 (DIO_11); also elsewhere on the board
/gpio/SPI_SCLK: U4.19 (DIO_13); also elsewhere on the board
/gpio/SPKR: U4.43 (DIO_30); also elsewhere on the board
/gpio/TEST_BLUE: U4.37 (DIO_24); also elsewhere on the board
/gpio/TEST_BUTTON: U4.32 (DIO_22); also elsewhere on the board
/gpio/TEST_GREEN: U4.36 (DIO_23); also elsewhere on the board
/gpio/VBAT_READ: U4.38 (DIO_25); also elsewhere on the board
GND: AE1.2 (PCB_Trace), B1.2, C1.2, C2.2, C3.2, C4.2, C5.2, C6.2, C7.2, C8.2, C9.2, C10.2, C11.2, C12.2, C13.2, C15.2, C17.2, C18.2, C19.2, C20.2, C21.2, C22.2, C23.2, J2.3 (GND), J2.5 (GND), J2.9 (GNDDetect), J3.1, L2.1, SW1.2, U1.1 (GND), U2.1 (GND), U3.1 (GND), U3.2 (GND), U4.49 (EGP), X1.2, X1.4; also elsewhere on the board
unnamed: D1.2 (A), D2.2 (A), R1.2, U4.35 (RESET_N)
unnamed: D1.1 (K), U3.3 (RESET_N)
unnamed: D2.1 (K), J2.10 (~RESET)
unnamed: J2.4 (SWCLK/TCK), U4.25 (JTAG_TCKC)
unnamed: J2.2 (SWDIO/TMS), U4.24 (JTAG_TMSC)
unnamed: B1.3, SW3.1 (A)
unnamed: B1.1, SW3.2 (B)
unnamed: SW1.1, U3.4 (MR_N)
unnamed: L1.1, U4.33 (DCDC_SW)
unnamed: C23.1, U4.23 (DCOUPL)
unnamed: C10.1, C11.1, C12.1, L1.2, U4.45 (VDDR), U4.48 (VDDR_RF)
unnamed: C17.1, U4.3 (X32K_Q1), X2.2
unnamed: C22.1, U4.4 (X32K_Q2), X2.1
unnamed: C15.1, U4.46 (X48M_N), X1.1
unnamed: C13.1, U4.47 (X48M_P), X1.3

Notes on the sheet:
power management
JTAG connector
crystals
Pin 22
C_{mc}=7uF
tuning caps
Pin 44
lowpass pi matching network
C0G/NP0 caps
X5R/X7R caps
C_{T}=2uF
RF ground
Pin 48
Pin 45
C_{L}=7uF
Pin 34
servo ground
analog ground
digital ground (omitted elsewhere)
Pin 13
balun

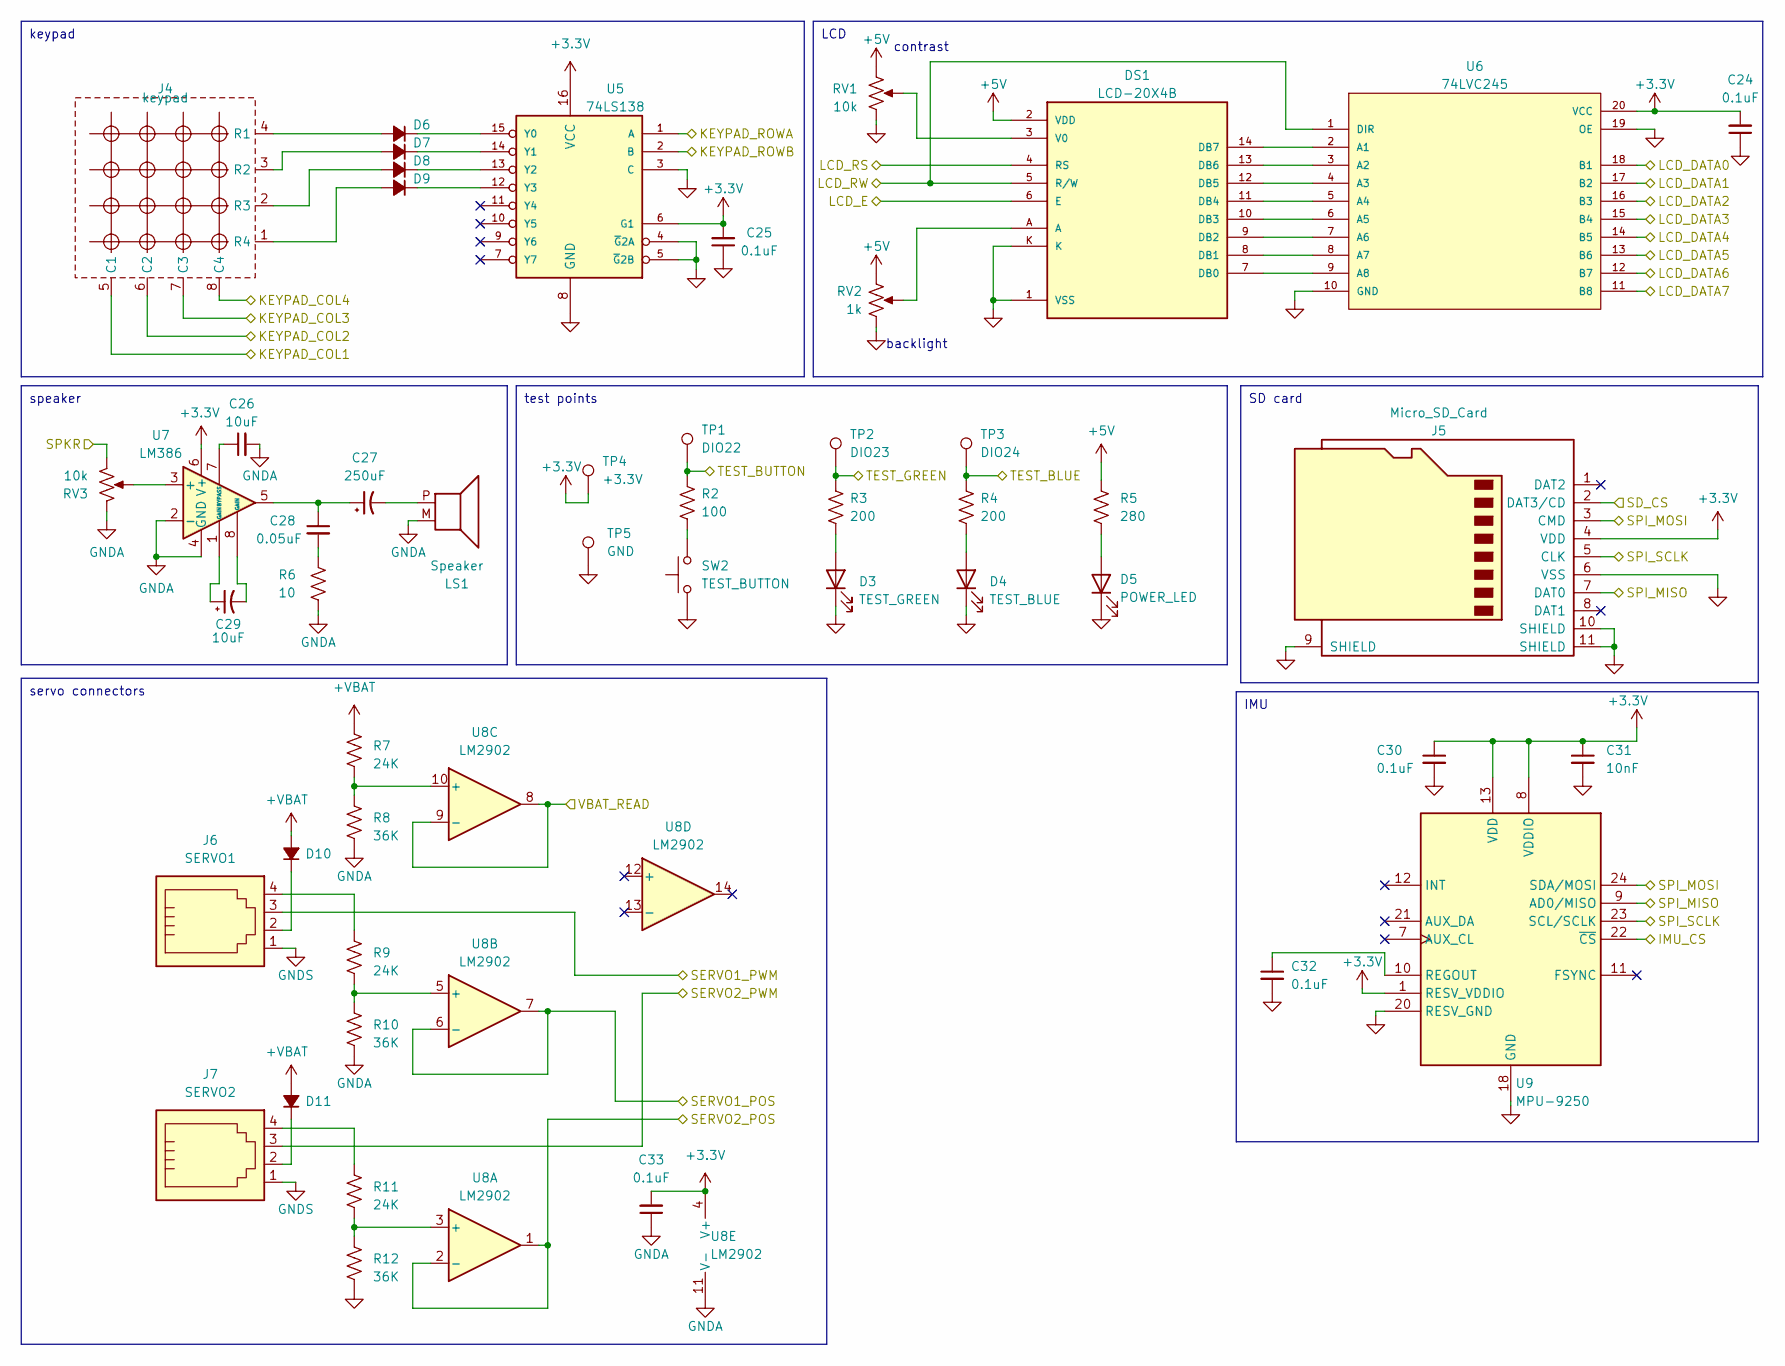
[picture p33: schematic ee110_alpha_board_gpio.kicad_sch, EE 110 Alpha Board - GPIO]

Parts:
C24, C25, C30, C32, C33: 0.1uF; C_0805_2012Metric_Pad1.18x1.45mm_HandSolder
C26: 10uF; C_0805_2012Metric_Pad1.18x1.45mm_HandSolder
C27: 250uF; CP_EIA-2012-12_Kemet-R_Pad1.30x1.05mm_HandSolder
C28: 0.05uF; C_0805_2012Metric_Pad1.18x1.45mm_HandSolder
C29: 10uF; CP_EIA-2012-12_Kemet-R_Pad1.30x1.05mm_HandSolder
C31: 10nF; C_0805_2012Metric_Pad1.18x1.45mm_HandSolder
D3: TEST_GREEN; LED_0805_2012Metric_Pad1.15x1.40mm_HandSolder
D4: TEST_BLUE; LED_0805_2012Metric_Pad1.15x1.40mm_HandSolder
D5: POWER_LED; LED_D3.0mm
D6, D7, D8, D9: D_Small_Filled; D_SOD-323F
D10, D11: D_Small_Filled; D_DO-15_P12.70mm_Horizontal
DS1: LCD-20X4B; WINSTAR-WH1604A; PARTREV N/A
J4: keypad; 4x4_Keypad
J5: Micro_SD_Card; microSD_HC_Hirose_DM3D-SF
J6: SERVO1; JST_XH_S4B-XH-A-1_1x04_P2.50mm_Horizontal
J7: SERVO2; JST_XH_S4B-XH-A-1_1x04_P2.50mm_Horizontal
LS1: Speaker; SPKR_CVS-1508
R2: 100; R_0805_2012Metric_Pad1.20x1.40mm_HandSolder
R3, R4: 200; R_0805_2012Metric_Pad1.20x1.40mm_HandSolder
R5: 280; R_0805_2012Metric_Pad1.20x1.40mm_HandSolder
R6: 10; R_0805_2012Metric_Pad1.20x1.40mm_HandSolder
R7, R9, R11: 24K; R_0805_2012Metric_Pad1.20x1.40mm_HandSolder
R8, R10, R12: 36K; R_0805_2012Metric_Pad1.20x1.40mm_HandSolder
RV1, RV3: 10k; Potentiometer_Bourns_3296P_Horizontal
RV2: 1k; Potentiometer_Bourns_3296P_Horizontal
SW2: TEST_BUTTON; SW_SPST_TL3342
TP1: DIO22; TestPoint_THTPad_2.0x2.0mm_Drill1.0mm
TP2: DIO23; TestPoint_THTPad_2.0x2.0mm_Drill1.0mm
TP3: DIO24; TestPoint_THTPad_2.0x2.0mm_Drill1.0mm
TP4: +3.3V; TestPoint_THTPad_2.0x2.0mm_Drill1.0mm
TP5: GND; TestPoint_THTPad_2.0x2.0mm_Drill1.0mm
U5: 74LS138; SOIC-16_3.9x9.9mm_P1.27mm
U6: 74LVC245; SOIC-20W_7.5x15.4mm_P1.27mm
U7: LM386; DIP-8_W7.62mm
U8: LM2902; SOIC-14_3.9x8.7mm_P1.27mm
U9: MPU-9250; QFN-24-1EP_3x3mm_P0.4mm_EP1.75x1.6mm

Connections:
+3.3V: C24.2, C25.2, C30.1, C31.1, C33.2, J5.4 (VDD), TP4.1, U5.6 (G1), U5.16 (VCC), U6.20 (VCC), U7.6 (V+), U8.4 (V+), U9.1 (RESV_VDDIO), U9.8 (VDDIO), U9.13 (VDD); also elsewhere on the board
+5V: DS1.2 (VDD), R5.1, RV1.1, RV2.1; also elsewhere on the board
+VBAT: D10.2 (A), D11.2 (A), R7.1; also elsewhere on the board
/gpio/IMU_CS: U9.22 (~CS); also elsewhere on the board
/gpio/KEYPAD_COL1: J4.5 (C1); also elsewhere on the board
/gpio/KEYPAD_COL2: J4.6 (C2); also elsewhere on the board
/gpio/KEYPAD_COL3: J4.7 (C3); also elsewhere on the board
/gpio/KEYPAD_COL4: J4.8 (C4); also elsewhere on the board
/gpio/KEYPAD_ROWA: U5.1 (A); also elsewhere on the board
/gpio/KEYPAD_ROWB: U5.2 (B); also elsewhere on the board
/gpio/LCD_DATA0: U6.18 (B1); also elsewhere on the board
/gpio/LCD_DATA1: U6.17 (B2); also elsewhere on the board
/gpio/LCD_DATA2: U6.16 (B3); also elsewhere on the board
/gpio/LCD_DATA3: U6.15 (B4); also elsewhere on the board
/gpio/LCD_DATA4: U6.14 (B5); also elsewhere on the board
/gpio/LCD_DATA5: U6.13 (B6); also elsewhere on the board
/gpio/LCD_DATA6: U6.12 (B7); also elsewhere on the board
/gpio/LCD_DATA7: U6.11 (B8); also elsewhere on the board
/gpio/LCD_E: DS1.6 (E); also elsewhere on the board
/gpio/LCD_RS: DS1.4 (RS); also elsewhere on the board
/gpio/LCD_RW: DS1.5 (R/W), U6.1 (DIR); also elsewhere on the board
/gpio/SD_CS: J5.2 (DAT3/CD); also elsewhere on the board
/gpio/SERVO1_POS: U8.6 (-), U8.7; also elsewhere on the board
/gpio/SERVO1_PWM: J6.3; also elsewhere on the board
/gpio/SERVO2_POS: U8.1, U8.2 (-); also elsewhere on the board
/gpio/SERVO2_PWM: J7.3; also elsewhere on the board
/gpio/SPI_MISO: J5.7 (DAT0), U9.9 (AD0/MISO); also elsewhere on the board
/gpio/SPI_MOSI: J5.3 (CMD), U9.24 (SDA/MOSI); also elsewhere on the board
/gpio/SPI_SCLK: J5.5 (CLK), U9.23 (SCL/SCLK); also elsewhere on the board
/gpio/SPKR: RV3.3; also elsewhere on the board
/gpio/TEST_BLUE: R4.2, TP3.1; also elsewhere on the board
/gpio/TEST_BUTTON: R2.2, TP1.1; also elsewhere on the board
/gpio/TEST_GREEN: R3.2, TP2.1; also elsewhere on the board
/gpio/VBAT_READ: U8.8, U8.9 (-); also elsewhere on the board
GND: C24.1, C25.1, C26.2, C30.2, C31.2, C32.2, C33.1, D3.1 (K), D4.1 (K), D5.1 (K), DS1.1 (VSS), DS1.K, J5.6 (VSS), J5.9 (SHIELD), J5.10 (SHIELD), J5.11 (SHIELD), J6.1, J7.1, LS1.M (2), R6.2, R8.2, R10.2, R12.2, RV1.3, RV2.3, RV3.1, SW2.1, TP5.1, U5.3 (C), U5.4 (~G2A), U5.5 (~G2B), U5.8 (GND), U6.10 (GND), U6.19 (OE), U7.2 (-), U7.4 (GND), U8.11 (V-), U9.18 (GND), U9.20 (RESV_GND); also elsewhere on the board
unnamed: C27.1, C28.1, U7.5
unnamed: C28.2, R6.1
unnamed: C29.1, U7.1 (GAIN)
unnamed: C29.2, U7.8 (GAIN)
unnamed: D3.2 (A), R3.1
unnamed: D4.2 (A), R4.1
unnamed: D5.2 (A), R5.2
unnamed: D6.2 (A), J4.4 (R1)
unnamed: D6.1 (K), U5.15 (Y0)
unnamed: D7.2 (A), J4.3 (R2)
unnamed: D7.1 (K), U5.14 (Y1)
unnamed: D8.2 (A), J4.2 (R3)
unnamed: D8.1 (K), U5.13 (Y2)
unnamed: D9.2 (A), J4.1 (R4)
unnamed: D9.1 (K), U5.12 (Y3)
unnamed: D10.1 (K), J6.2
unnamed: D11.1 (K), J7.2
unnamed: DS1.7 (DB0), U6.9 (A8)
unnamed: DS1.8 (DB1), U6.8 (A7)
unnamed: DS1.9 (DB2), U6.7 (A6)
unnamed: DS1.10 (DB3), U6.6 (A5)
unnamed: DS1.11 (DB4), U6.5 (A4)
unnamed: DS1.12 (DB5), U6.4 (A3)
unnamed: DS1.13 (DB6), U6.3 (A2)
unnamed: DS1.14 (DB7), U6.2 (A1)
unnamed: DS1.A, RV2.2
unnamed: DS1.3 (V0), RV1.2
unnamed: J6.4, R9.1
unnamed: J7.4, R11.1
unnamed: C27.2, LS1.P (1)
unnamed: R2.1, SW2.2
unnamed: RV3.2, U7.3 (+)
unnamed: C26.1, U7.7 (BYPASS)
unnamed: R11.2, R12.1, U8.3 (+)
unnamed: R9.2, R10.1, U8.5 (+)
unnamed: R7.2, R8.1, U8.10 (+)
unnamed: C32.1, U9.10 (REGOUT)

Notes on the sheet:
keypad
SD card
servo connectors
speaker
test points
LCD
IMU
backlight
contrast

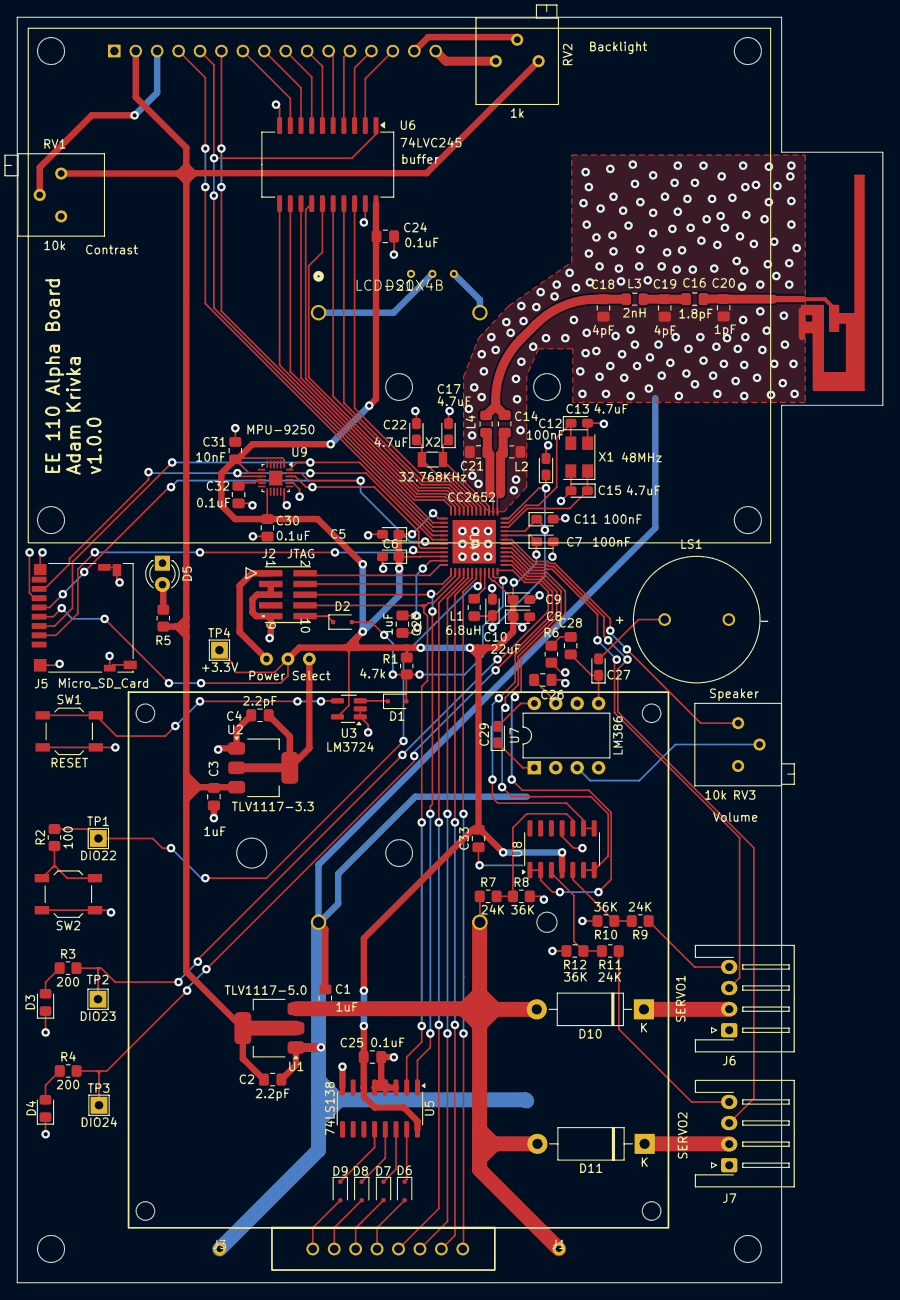
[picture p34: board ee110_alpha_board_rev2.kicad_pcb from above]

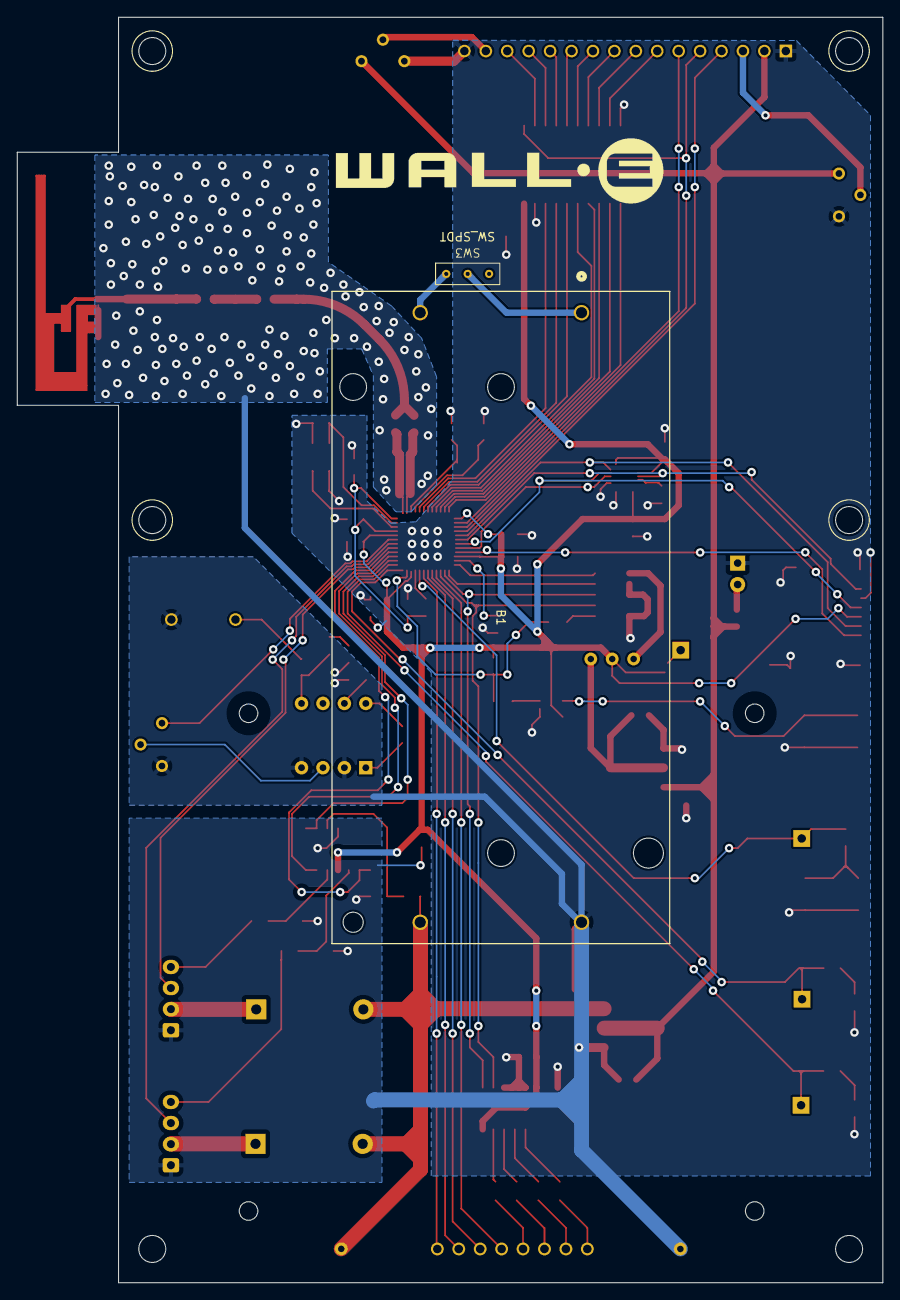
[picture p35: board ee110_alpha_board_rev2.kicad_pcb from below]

Board: 2 copper layers, 102.6 x 150.0 mm, 93 parts (2 on the bottom side), 94 nets.

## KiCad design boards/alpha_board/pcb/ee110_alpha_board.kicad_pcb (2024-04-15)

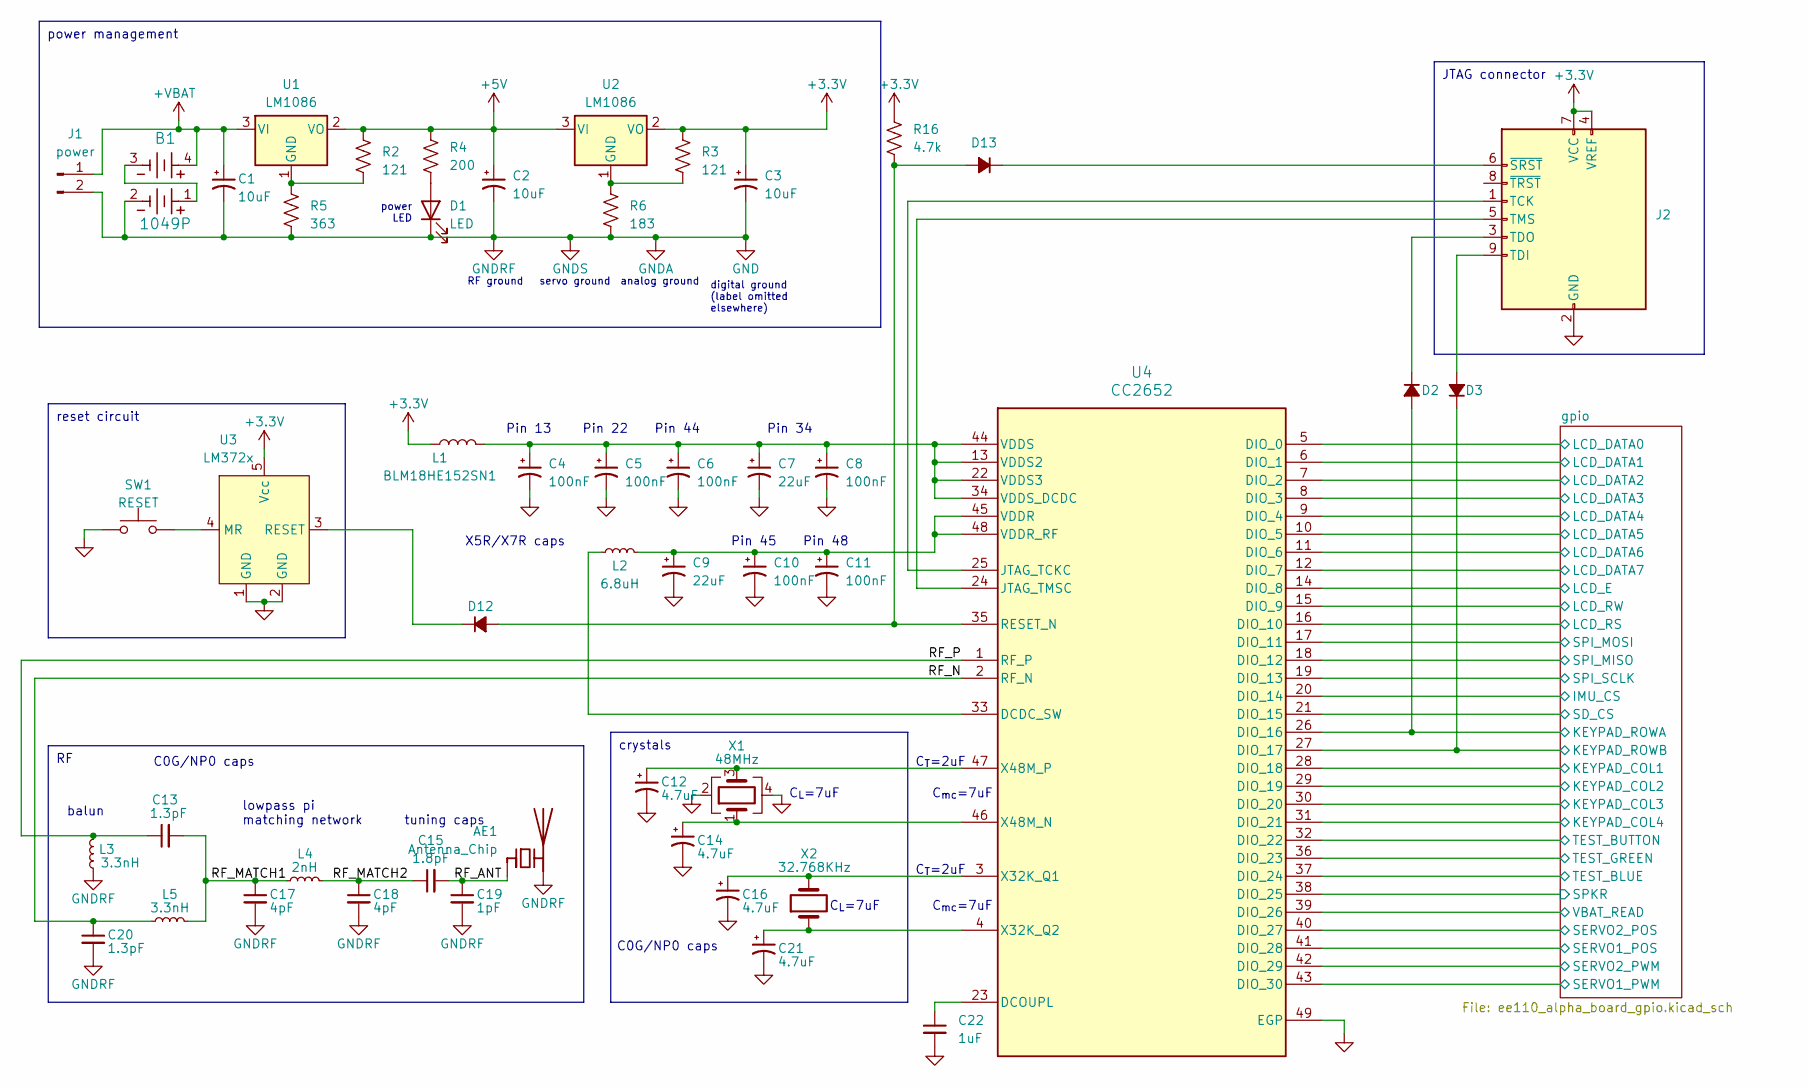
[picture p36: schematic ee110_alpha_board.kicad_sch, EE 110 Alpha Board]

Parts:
AE1: Antenna_Chip; EE110_Antenna
B1: 1049P; 1049P_KEY
C1, C2, C3: 10uF; CP_EIA-1608-08_AVX-J_Pad1.25x1.05mm_HandSolder
C4, C5, C6, C8, C10, C11: 100nF; CP_EIA-1608-08_AVX-J_Pad1.25x1.05mm_HandSolder
C7, C9: 22uF; CP_EIA-1608-08_AVX-J_Pad1.25x1.05mm_HandSolder
C12, C14, C16, C21: 4.7uF; CP_EIA-1608-08_AVX-J_Pad1.25x1.05mm_HandSolder
C13, C20: 1.3pF; C_0805_2012Metric_Pad1.18x1.45mm_HandSolder
C15: 1.8pF; C_0805_2012Metric_Pad1.18x1.45mm_HandSolder
C17, C18: 4pF; C_0805_2012Metric_Pad1.18x1.45mm_HandSolder
C19: 1pF; C_0805_2012Metric_Pad1.18x1.45mm_HandSolder
C22: 1uF; C_0603_1608Metric_Pad1.08x0.95mm_HandSolder
D1: LED; LED_D3.0mm
D2, D3, D12, D13: D_Small_Filled; D_0603_1608Metric_Pad1.05x0.95mm_HandSolder
J1: power; My_Power_Connector
J2: JTAG; CON10_2X5_DUK_FTSH_SAI
L1: BLM18HE152SN1; L_7.3x7.3_H3.5
L2: 6.8uH; L_0603_1608Metric_Pad1.05x0.95mm_HandSolder
L3, L5: 3.3nH; L_0805_2012Metric_Pad1.15x1.40mm_HandSolder
L4: 2nH; L_0805_2012Metric_Pad1.15x1.40mm_HandSolder
R2, R3: 121; R_0603_1608Metric_Pad0.98x0.95mm_HandSolder
R4: 200; R_0603_1608Metric_Pad0.98x0.95mm_HandSolder
R5: 363; R_0603_1608Metric_Pad0.98x0.95mm_HandSolder
R6: 183; R_0603_1608Metric_Pad0.98x0.95mm_HandSolder
R16: 4.7k; R_0603_1608Metric_Pad0.98x0.95mm_HandSolder
SW1: RESET; SW_SPST_TL3342
U1, U2: LM1086; TO-263-3_TabPin2
U3: LM372x; SOT-23-5
U4: CC2652; RGZ0048A_NV
X1: 48MHz; Crystal_SMD_2016-4Pin_2.0x1.6mm
X2: 32.768KHz; Crystal_SMD_3215-2Pin_3.2x1.5mm

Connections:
+3.3V: C3.1, J2.4 (VREF), J2.7 (VCC), L1.1, R3.1, R16.1, U2.2 (VO), U3.5 (Vcc); also elsewhere on the board
+5V: C2.1, R2.1, R4.1, U1.2 (VO), U2.3 (VI); also elsewhere on the board
+VBAT: B1.4, C1.1, J1.1, U1.3 (VI); also elsewhere on the board
/RF_ANT: AE1.1 (FEED), C15.2, C19.1
/RF_MATCH1: C13.2, C17.1, L4.1, L5.2
/RF_MATCH2: C15.1, C18.1, L4.2
/RF_N: C20.1, L5.1, U4.2 (RF_N)
/RF_P: C13.1, L3.2, U4.1 (RF_P)
/gpio/IMU_CS: U4.20 (DIO_14); also elsewhere on the board
/gpio/KEYPAD_COL1: U4.28 (DIO_18); also elsewhere on the board
/gpio/KEYPAD_COL2: U4.29 (DIO_19); also elsewhere on the board
/gpio/KEYPAD_COL3: U4.30 (DIO_20); also elsewhere on the board
/gpio/KEYPAD_COL4: U4.31 (DIO_21); also elsewhere on the board
/gpio/KEYPAD_ROWA: D2.2 (A), U4.26 (DIO_16); also elsewhere on the board
/gpio/KEYPAD_ROWB: D3.1 (K), U4.27 (DIO_17); also elsewhere on the board
/gpio/LCD_DATA0: U4.5 (DIO_0); also elsewhere on the board
/gpio/LCD_DATA1: U4.6 (DIO_1); also elsewhere on the board
/gpio/LCD_DATA2: U4.7 (DIO_2); also elsewhere on the board
/gpio/LCD_DATA3: U4.8 (DIO_3); also elsewhere on the board
/gpio/LCD_DATA4: U4.9 (DIO_4); also elsewhere on the board
/gpio/LCD_DATA5: U4.10 (DIO_5); also elsewhere on the board
/gpio/LCD_DATA6: U4.11 (DIO_6); also elsewhere on the board
/gpio/LCD_DATA7: U4.12 (DIO_7); also elsewhere on the board
/gpio/LCD_E: U4.14 (DIO_8); also elsewhere on the board
/gpio/LCD_RS: U4.16 (DIO_10); also elsewhere on the board
/gpio/LCD_RW: U4.15 (DIO_9); also elsewhere on the board
/gpio/SD_CS: U4.21 (DIO_15); also elsewhere on the board
/gpio/SERVO1_POS: U4.41 (DIO_28); also elsewhere on the board
/gpio/SERVO1_PWM: U4.43 (DIO_30); also elsewhere on the board
/gpio/SERVO2_POS: U4.40 (DIO_27); also elsewhere on the board
/gpio/SERVO2_PWM: U4.42 (DIO_29); also elsewhere on the board
/gpio/SPI_MISO: U4.18 (DIO_12); also elsewhere on the board
/gpio/SPI_MOSI: U4.17 (DIO_11); also elsewhere on the board
/gpio/SPI_SCLK: U4.19 (DIO_13); also elsewhere on the board
/gpio/SPKR: U4.38 (DIO_25); also elsewhere on the board
/gpio/TEST_BLUE: U4.37 (DIO_24); also elsewhere on the board
/gpio/TEST_BUTTON: U4.32 (DIO_22); also elsewhere on the board
/gpio/TEST_GREEN: U4.36 (DIO_23); also elsewhere on the board
/gpio/VBAT_READ: U4.39 (DIO_26); also elsewhere on the board
GND: AE1.2 (PCB_Trace), B1.2, C1.2, C2.2, C3.2, C4.2, C5.2, C6.2, C7.2, C8.2, C9.2, C10.2, C11.2, C12.2, C14.2, C16.2, C17.2, C18.2, C19.2, C20.2, C21.2, C22.2, D1.1 (K), J1.2, J2.2 (GND), J2.10 (GND), L3.1, R5.2, R6.2, SW1.1, U3.1 (GND), U3.2 (GND), U4.49 (EGP), X1.2, X1.4; also elsewhere on the board
unnamed: B1.1, B1.3
unnamed: D1.2 (A), R4.2
unnamed: D2.1 (K), J2.3 (TDO)
unnamed: D3.2 (A), J2.9 (TDI)
unnamed: D12.2 (A), D13.2 (A), R16.2, U4.35 (RESET_N)
unnamed: D12.1 (K), U3.3 (RESET)
unnamed: D13.1 (K), J2.6 (~SRST)
unnamed: J2.1 (TCK), U4.25 (JTAG_TCKC)
unnamed: J2.5 (TMS), U4.24 (JTAG_TMSC)
unnamed: R2.2, R5.1, U1.1 (GND)
unnamed: R3.2, R6.1, U2.1 (GND)
unnamed: SW1.2, U3.4 (MR)
unnamed: L2.1, U4.33 (DCDC_SW)
unnamed: C22.1, U4.23 (DCOUPL)
unnamed: C9.1, C10.1, C11.1, L2.2, U4.45 (VDDR), U4.48 (VDDR_RF)
unnamed: C4.1, C5.1, C6.1, C7.1, C8.1, L1.2, U4.13 (VDDS2), U4.22 (VDDS3), U4.34 (VDDS_DCDC), U4.44 (VDDS)
unnamed: C16.1, U4.3 (X32K_Q1), X2.2
unnamed: C21.1, U4.4 (X32K_Q2), X2.1
unnamed: C14.1, U4.46 (X48M_N), X1.1
unnamed: C12.1, U4.47 (X48M_P), X1.3

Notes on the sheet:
reset circuit
power management
JTAG connector
crystals
Pin 22
power LED
C_{mc}=7uF
tuning caps
Pin 44
lowpass pi matching network
C0G/NP0 caps
X5R/X7R caps
C_{T}=2uF
RF ground
Pin 48
Pin 45
C_{L}=7uF
Pin 34
servo ground
analog ground
digital ground (label omitted elsewhere)
Pin 13
balun

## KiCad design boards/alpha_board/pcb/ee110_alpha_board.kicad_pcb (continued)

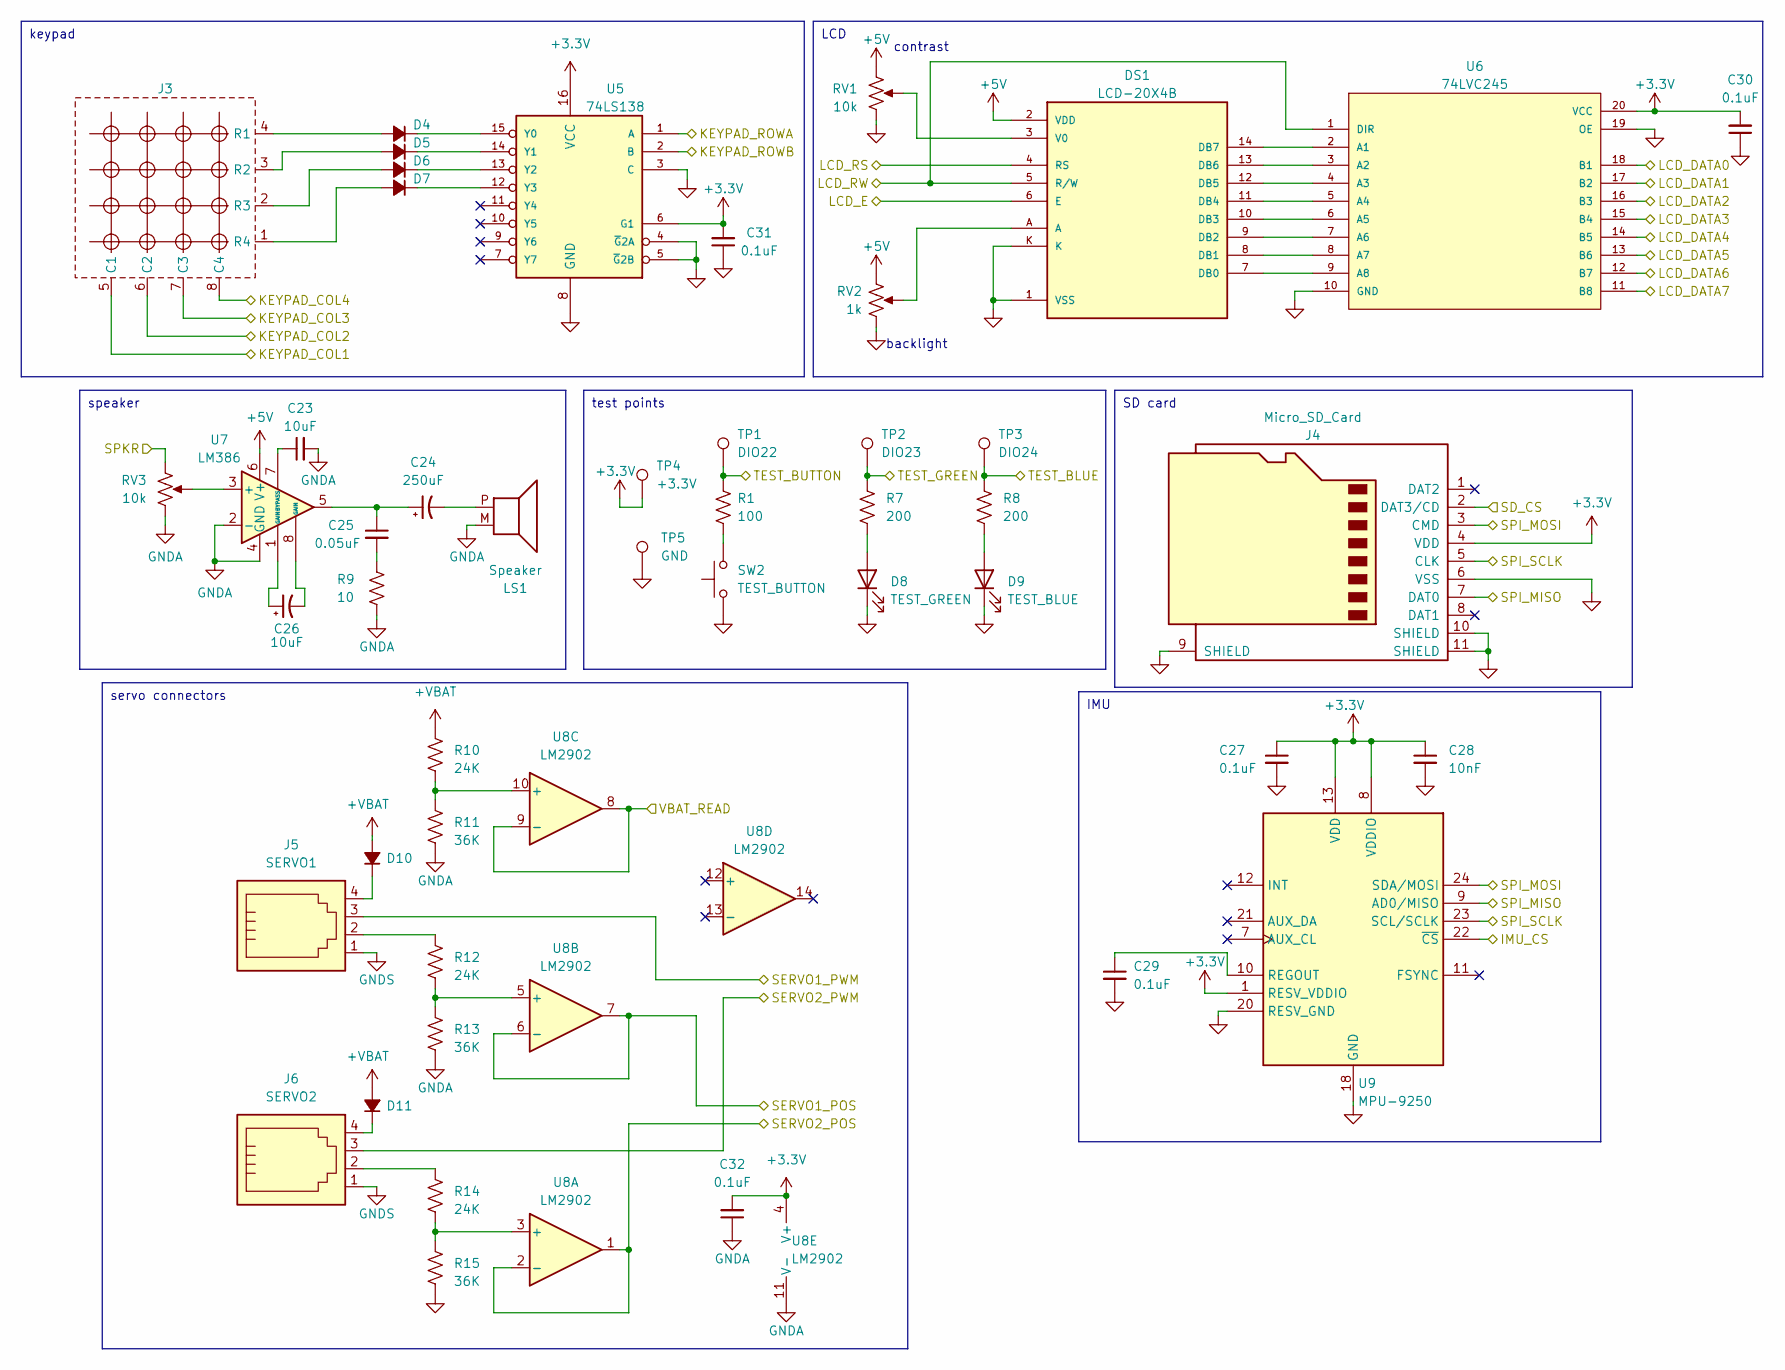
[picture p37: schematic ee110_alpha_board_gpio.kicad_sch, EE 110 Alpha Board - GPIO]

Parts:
C23, C26: 10uF; C_0603_1608Metric_Pad1.08x0.95mm_HandSolder
C24: 250uF; C_0603_1608Metric_Pad1.08x0.95mm_HandSolder
C25: 0.05uF; C_0603_1608Metric_Pad1.08x0.95mm_HandSolder
C27, C29, C30, C31, C32: 0.1uF; C_0603_1608Metric_Pad1.08x0.95mm_HandSolder
C28: 10nF; C_0603_1608Metric_Pad1.08x0.95mm_HandSolder
D4, D5, D6, D7: D_Small_Filled; D_0603_1608Metric_Pad1.05x0.95mm_HandSolder
D8: TEST_GREEN; LED_0603_1608Metric_Pad1.05x0.95mm_HandSolder
D9: TEST_BLUE; LED_0603_1608Metric_Pad1.05x0.95mm_HandSolder
D10, D11: D_Small_Filled; D_1206_3216Metric_Pad1.42x1.75mm_HandSolder
DS1: LCD-20X4B; WINSTAR-WH1604A; PARTREV N/A
J3: 4x4_Keypad
J4: Micro_SD_Card; microSD_HC_Hirose_DM3D-SF
J5: SERVO1; JST_XH_S4B-XH-A-1_1x04_P2.50mm_Horizontal
J6: SERVO2; JST_XH_S4B-XH-A-1_1x04_P2.50mm_Horizontal
LS1: Speaker; SPKR_CVS-1508
R1: 100; R_0603_1608Metric_Pad0.98x0.95mm_HandSolder
R7, R8: 200; R_0603_1608Metric_Pad0.98x0.95mm_HandSolder
R9: 10; R_0603_1608Metric_Pad0.98x0.95mm_HandSolder
R10, R12, R14: 24K; R_0603_1608Metric_Pad0.98x0.95mm_HandSolder
R11, R13, R15: 36K; R_0603_1608Metric_Pad0.98x0.95mm_HandSolder
RV1, RV3: 10k; Potentiometer_Bourns_3296P_Horizontal
RV2: 1k; Potentiometer_Bourns_3296P_Horizontal
SW2: TEST_BUTTON; SW_SPST_TL3342
TP1: DIO22; TestPoint_THTPad_2.0x2.0mm_Drill1.0mm
TP2: DIO23; TestPoint_THTPad_2.0x2.0mm_Drill1.0mm
TP3: DIO24; TestPoint_THTPad_2.0x2.0mm_Drill1.0mm
TP4: +3.3V; TestPoint_THTPad_2.0x2.0mm_Drill1.0mm
TP5: GND; TestPoint_THTPad_2.0x2.0mm_Drill1.0mm
U5: 74LS138; SOIC-16_3.9x9.9mm_P1.27mm
U6: 74LVC245; SOIC-20W_7.5x15.4mm_P1.27mm
U7: LM386; DIP-8_W7.62mm
U8: LM2902; SOIC-14_3.9x8.7mm_P1.27mm
U9: MPU-9250; QFN-24-1EP_3x3mm_P0.4mm_EP1.75x1.6mm

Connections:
+3.3V: C27.1, C28.1, C30.2, C31.2, C32.2, J4.4 (VDD), TP4.1, U5.6 (G1), U5.16 (VCC), U6.20 (VCC), U8.4 (V+), U9.1 (RESV_VDDIO), U9.8 (VDDIO), U9.13 (VDD); also elsewhere on the board
+5V: DS1.2 (VDD), RV1.1, RV2.1, U7.6 (V+); also elsewhere on the board
+VBAT: D10.2 (A), D11.2 (A), R10.1; also elsewhere on the board
/gpio/IMU_CS: U9.22 (~CS); also elsewhere on the board
/gpio/KEYPAD_COL1: J3.5 (C1); also elsewhere on the board
/gpio/KEYPAD_COL2: J3.6 (C2); also elsewhere on the board
/gpio/KEYPAD_COL3: J3.7 (C3); also elsewhere on the board
/gpio/KEYPAD_COL4: J3.8 (C4); also elsewhere on the board
/gpio/KEYPAD_ROWA: U5.1 (A); also elsewhere on the board
/gpio/KEYPAD_ROWB: U5.2 (B); also elsewhere on the board
/gpio/LCD_DATA0: U6.18 (B1); also elsewhere on the board
/gpio/LCD_DATA1: U6.17 (B2); also elsewhere on the board
/gpio/LCD_DATA2: U6.16 (B3); also elsewhere on the board
/gpio/LCD_DATA3: U6.15 (B4); also elsewhere on the board
/gpio/LCD_DATA4: U6.14 (B5); also elsewhere on the board
/gpio/LCD_DATA5: U6.13 (B6); also elsewhere on the board
/gpio/LCD_DATA6: U6.12 (B7); also elsewhere on the board
/gpio/LCD_DATA7: U6.11 (B8); also elsewhere on the board
/gpio/LCD_E: DS1.6 (E); also elsewhere on the board
/gpio/LCD_RS: DS1.4 (RS); also elsewhere on the board
/gpio/LCD_RW: DS1.5 (R/W), U6.1 (DIR); also elsewhere on the board
/gpio/SD_CS: J4.2 (DAT3/CD); also elsewhere on the board
/gpio/SERVO1_POS: U8.6 (-), U8.7; also elsewhere on the board
/gpio/SERVO1_PWM: J5.3; also elsewhere on the board
/gpio/SERVO2_POS: U8.1, U8.2 (-); also elsewhere on the board
/gpio/SERVO2_PWM: J6.3; also elsewhere on the board
/gpio/SPI_MISO: J4.7 (DAT0), U9.9 (AD0/MISO); also elsewhere on the board
/gpio/SPI_MOSI: J4.3 (CMD), U9.24 (SDA/MOSI); also elsewhere on the board
/gpio/SPI_SCLK: J4.5 (CLK), U9.23 (SCL/SCLK); also elsewhere on the board
/gpio/SPKR: RV3.1; also elsewhere on the board
/gpio/TEST_BLUE: R8.2, TP3.1; also elsewhere on the board
/gpio/TEST_BUTTON: R1.2, TP1.1; also elsewhere on the board
/gpio/TEST_GREEN: R7.2, TP2.1; also elsewhere on the board
/gpio/VBAT_READ: U8.8, U8.9 (-); also elsewhere on the board
GND: C23.2, C27.2, C28.2, C29.2, C30.1, C31.1, C32.1, D8.1 (K), D9.1 (K), DS1.1 (VSS), DS1.K, J4.6 (VSS), J4.9 (SHIELD), J4.10 (SHIELD), J4.11 (SHIELD), J5.1, J6.1, LS1.M (2), R9.2, R11.2, R13.2, R15.2, RV1.3, RV2.3, RV3.3, SW2.1, TP5.1, U5.3 (C), U5.4 (~G2A), U5.5 (~G2B), U5.8 (GND), U6.10 (GND), U6.19 (OE), U7.2 (-), U7.4 (GND), U8.11 (V-), U9.18 (GND), U9.20 (RESV_GND); also elsewhere on the board
unnamed: C24.1, C25.1, U7.5
unnamed: C25.2, R9.1
unnamed: C26.1, U7.1 (GAIN)
unnamed: C26.2, U7.8 (GAIN)
unnamed: D4.2 (A), J3.4 (R1)
unnamed: D4.1 (K), U5.15 (Y0)
unnamed: D5.2 (A), J3.3 (R2)
unnamed: D5.1 (K), U5.14 (Y1)
unnamed: D6.2 (A), J3.2 (R3)
unnamed: D6.1 (K), U5.13 (Y2)
unnamed: D7.2 (A), J3.1 (R4)
unnamed: D7.1 (K), U5.12 (Y3)
unnamed: D8.2 (A), R7.1
unnamed: D9.2 (A), R8.1
unnamed: D10.1 (K), J5.4
unnamed: D11.1 (K), J6.4
unnamed: DS1.7 (DB0), U6.9 (A8)
unnamed: DS1.8 (DB1), U6.8 (A7)
unnamed: DS1.9 (DB2), U6.7 (A6)
unnamed: DS1.10 (DB3), U6.6 (A5)
unnamed: DS1.11 (DB4), U6.5 (A4)
unnamed: DS1.12 (DB5), U6.4 (A3)
unnamed: DS1.13 (DB6), U6.3 (A2)
unnamed: DS1.14 (DB7), U6.2 (A1)
unnamed: DS1.A, RV2.2
unnamed: DS1.3 (V0), RV1.2
unnamed: J5.2, R12.1
unnamed: J6.2, R14.1
unnamed: C24.2, LS1.P (1)
unnamed: R1.1, SW2.2
unnamed: RV3.2, U7.3 (+)
unnamed: C23.1, U7.7 (BYPASS)
unnamed: R14.2, R15.1, U8.3 (+)
unnamed: R12.2, R13.1, U8.5 (+)
unnamed: R10.2, R11.1, U8.10 (+)
unnamed: C29.1, U9.10 (REGOUT)

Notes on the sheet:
test points
keypad
SD card
servo connectors
speaker
LCD
IMU
backlight
contrast

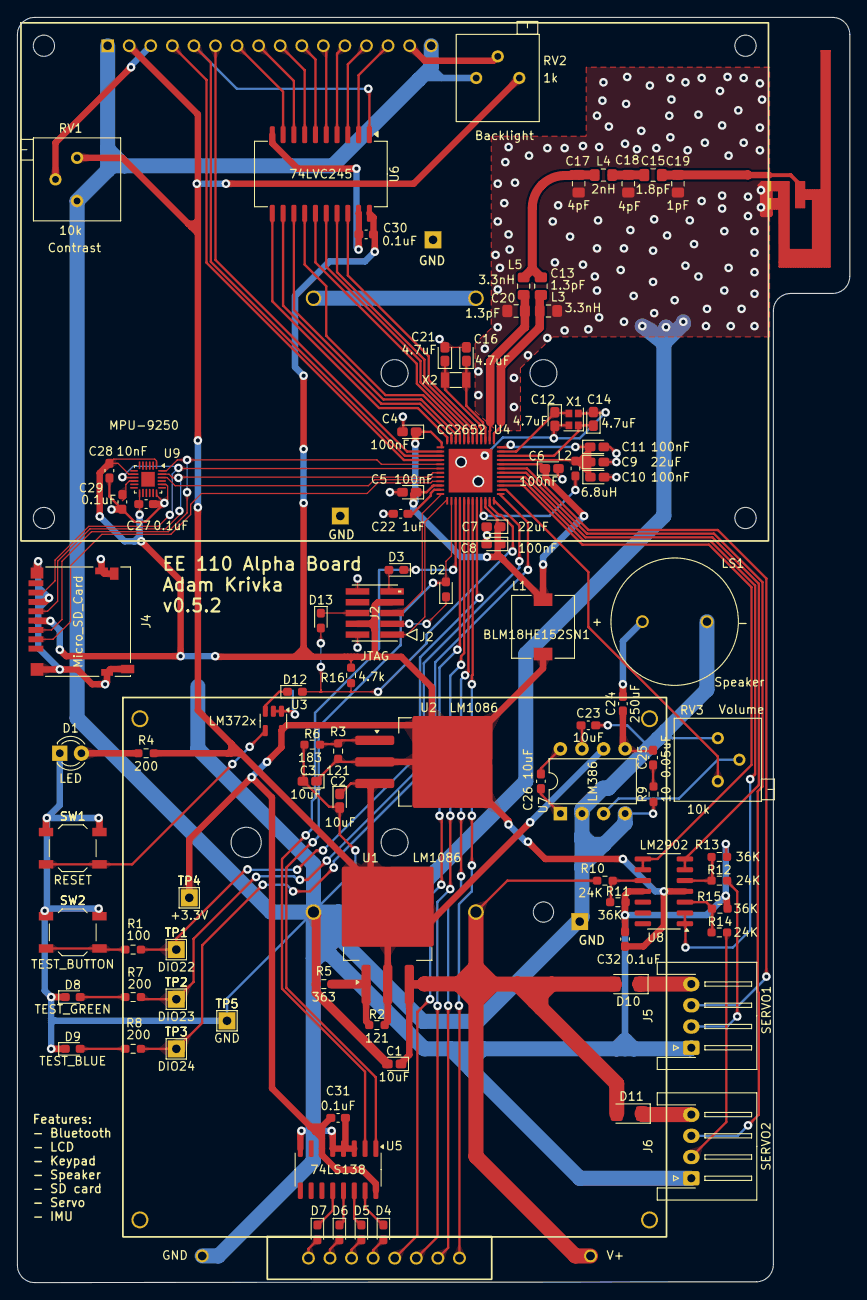
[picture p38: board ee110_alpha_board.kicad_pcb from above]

Board: 2 copper layers, 98.0 x 149.0 mm, 97 parts (1 on the bottom side), 96 nets.

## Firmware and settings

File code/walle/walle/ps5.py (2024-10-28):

#!/usr/bin/env python3
import rclpy
import time
from utils.printing import ros_print
from evdev import list_devices, InputDevice, ecodes
import threading
import numpy as np

from rclpy.node         import Node
from geometry_msgs.msg  import Twist
from std_msgs.msg import Int16MultiArray

RATE = 50.0  

class Ps5Node(Node):
    ADDRESS = 0x80
    FULL_FORWARD = 127
    FULL_BACKWARD = 0
    
    LY = 1
    LX = 0
    RX = 3
    RY = 4
    LT = 2
    RT = 5
    PY = 17
    PX = 16
    LB = 310
    RB = 311
    
    X = 304
    O = 305
    T = 307
    S = 308
    SPECIAL = 315
    
    LEFT_ARM =      0
    RIGHT_ARM =     1
    LOW_NECK =      2
    MID_NECK =      3
    HEAD_SWIVEL =   4
    LEFT_EYE =      5
    RIGHT_EYE =     6
    
    ALARM =         0
    EVA =           1
    TADA =          2
    WALLE =         3
    WOAH =          4

    def __init__(self, name):
        super().__init__(name)
            
        self.dev = InputDevice(list_devices()[0])
        self.cmdvel_pub = self.create_publisher(Twist, '/cmd_vel', 10)
        self.jointpos_pub = self.create_publisher(Int16MultiArray, '/joint_pos', 10)
        self.effects_pub = self.create_publisher(Int16MultiArray, '/effects', 10)
        self.speed = 0
        self.turn = 0
        self.forward = 0
        self.backward = 0
        self.left_arm = 90
        self.right_arm = 90
        self.joints = [0]*7
        self.joints[self.LEFT_ARM] = 90
        self.joints[self.RIGHT_ARM] = 90
        self.joints[self.HEAD_SWIVEL] = 90
        self.joints[self.LOW_NECK] = 50
        self.joints[self.MID_NECK] = 110
        self.joints[self.LEFT_EYE] = 90
        self.joints[self.RIGHT_EYE] = 90
        self.limits = {}
        self.limits[self.LEFT_EYE] = [60, 90]
        self.limits[self.RIGHT_EYE] = [90, 120]
        self.end = False
        self.effects = [0]*5
        self.ps5_thread = threading.Thread(target=self.read_ps5)
        self.ps5_thread.start()
        # Create a timer to keep calculating/sending commands.
        self.timer = self.create_timer(1 / RATE, self.send_vels)
        self.timer = self.create_timer(1 / RATE, self.send_pos)
        ros_print(self, 'PS5 node started')

    def read_ps5(self):
        for event in self.dev.read_loop():
            if event.type == ecodes.EV_ABS:
                self.update = time.time()
                # ros_print(self, event.code, event.value)
                if event.code == self.LX:
                    diff = -(event.value - 127)
                    if abs(diff) < 10: diff = 0
                    self.turn = diff
                elif event.code == self.LT:
                    self.backward = event.value
                elif event.code == self.RT:
                    self.forward = event.value
                elif event.code == self.RX:
                    diff = -(event.value - 127)
                    if abs(diff) < 10: diff = 0
                    self.joints[self.HEAD_SWIVEL] = diff / 128 * 45 + 90
                elif event.code == self.RY:
                    diff = -(event.value - 127)
                    if abs(diff) < 10: diff = 0
                    self.joints[self.MID_NECK] = diff / 128 * 50 + 110
                    diff = -(event.value - 127)
                    if abs(diff) < 10: diff = 0
                    self.joints[self.LOW_NECK] = diff / 128 * 20 + 90
                    # code in the dumbo kinematics
                elif event.code == self.PY:
                    # self.left_arm += 1/1000 * (-event.value)
                    # self.right_arm += 1/1000 * (event.value)
                    # self.left_arm = max(min(self.left_arm, 60), 120)
                    # self.right_arm = max(min(self.right_arm, 60), 120)
                    # self.joints[self.LEFT_ARM] = self.left_arm
                    # self.joints[self.RIGHT_ARM] = self.right_arm
                    self.joints[self.LEFT_ARM] = -event.value * 40 + 90
                    self.joints[self.RIGHT_ARM] = event.value * 40 + 90
                self.speed = (self.forward - self.backward) / 2
                  
            if event.type == ecodes.EV_KEY:
                if event.code == self.LB:
                    self.joints[self.LEFT_EYE] = 90 - event.value * 20
                    if self.LEFT_EYE in self.limits:
                        small, big = self.limits[self.LEFT_EYE]
                        self.joints[self.LEFT_EYE] = min(max(self.joints[self.LEFT_EYE], small), big)
                elif event.code == self.RB:
                    self.joints[self.RIGHT_EYE] = 90 + event.value * 20
                    if self.RIGHT_EYE in self.limits:
                        small, big = self.limits[self.RIGHT_EYE]
                        self.joints[self.RIGHT_EYE] = min(max(self.joints[self.RIGHT_EYE], small), big)
                elif event.code == self.X:
                    self.effects[self.WALLE] = event.value
                elif event.code == self.O:
                    self.effects[self.EVA] = event.value
                elif event.code == self.T:
                    self.effects[self.TADA] = event.value
                elif event.code == self.S:
                    self.effects[self.WOAH] = event.value
            if self.end:
                break
            
            msg = Int16MultiArray()
            msg.data = self.effects
            self.effects_pub.publish(msg)

    def send_pos(self):
        msg = Int16MultiArray()
        msg.data = np.array(self.joints).astype(int).tolist()
        self.jointpos_pub.publish(msg)
        
    def send_vels(self):
        msg = Twist()
        msg.linear.x = float(self.speed)
        msg.angular.z = float(self.turn)
        self.cmdvel_pub.publish(msg)
    
    # Shutdown
    def shutdown(self):
        # No particular cleanup, just shut down the node.
        self.end = True
        self.read_ps5.join()
        self.destroy_node()

#
#   Main Code
#
def main(args=None):

    # Initialize ROS.
    rclpy.init(args=args)

    # Instantiate the detector node.
    node = Ps5Node('play')

    # Spin the node until interrupted.
    rclpy.spin(node)

    # Shutdown the node and ROS.
    node.shutdown()
    rclpy.shutdown()

if __name__ == "__main__":
    main()

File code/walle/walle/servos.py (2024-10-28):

#!/usr/bin/env python3
import rclpy
import time
from utils.printing import ros_print
from utils.servo import MultiServo
from evdev import list_devices, InputDevice, categorize, ecodes
import threading
import numpy as np

from rclpy.node         import Node
from sensor_msgs.msg    import Image
from geometry_msgs.msg  import Point, Pose, PoseArray, Vector3, Twist
from nav_msgs.msg       import Odometry
from visualization_msgs.msg import Marker, MarkerArray
from std_msgs.msg import Int16MultiArray

RATE = 50.0  

class ServoNode(Node):
    LEFT_ARM =      0
    RIGHT_ARM =     1
    LOW_NECK =      2
    MID_NECK =      3
    HEAD_SWIVEL =   4
    LEFT_EYE =      5
    RIGHT_EYE =     6

    def __init__(self, name):
        super().__init__(name)
            
        self.joints = [0]*7
        self.joints[self.LEFT_ARM] = 90
        self.joints[self.RIGHT_ARM] = 90
        self.joints[self.HEAD_SWIVEL] = 90
        self.joints[self.LOW_NECK] = 50
        self.joints[self.MID_NECK] = 110
        self.joints[self.LEFT_EYE] = 90
        self.joints[self.RIGHT_EYE] = 90
        
        self.theta_max = 360 * 2
        self.ms = MultiServo(init_angles=self.joints)
        self.update = time.time()
        self.start = time.time()
        self.T = 0.1
        self.dt = 0.1
        self.last_t = time.time()
        self.create_subscription(Int16MultiArray, '/joint_pos', self.servo_pos_cb, 10)
        self.cycles = 0
        self.last = time.time()
        # # Create a timer to keep calculating/sending commands.
        self.timer = self.create_timer(1 / RATE, self.send_cmd)
        ros_print(self, 'Servo node started')

    def servo_pos_cb(self, msg: Int16MultiArray):
        assert(len(msg.data) == 7)
        self.update = time.time()
        self.filter_update(list(msg.data))
    
    def abs_min(self, u, bound):
        ret = min(abs(u), abs(bound))
        if u < 0:
            return -abs(ret)
        else:
            return abs(ret)
        
    def filter_update(self, new_joints):
        self.dt = min(time.time() - self.last, self.T)
        # ros_print(self, time.time() - self.last)
        self.last = time.time()
        for i in range(len(self.joints)):
            self.joints[i] += self.dt / self.T * (self.abs_min(new_joints[i] - self.joints[i], self.theta_max * self.dt))
            
    def send_cmd(self):
        if time.time() - self.update >= 1:
            return
        # self.cycles += 1
        # self.joints[0] = 90 * np.sin(time.time() - self.start) + 90
        # if time.time() - self.last > 1:
        #     ros_print(self, self.cycles)
        #     self.cycles = 0
        #     self.last = time.time()
                 
        self.ms.angles = self.joints
        ros_print(self, self.joints)
        self.ms.cmd_angles()
        # ros_print(self, self.ms.pwms)
    
    # Shutdown
    def shutdown(self):
        # No particular cleanup, just shut down the node.
        self.destroy_node()

#
#   Main Code
#
def main(args=None):

    # Initialize ROS.
    rclpy.init(args=args)

    # Instantiate the detector node.
    node = ServoNode('servos')

    # Spin the node until interrupted.
    rclpy.spin(node)

    # Shutdown the node and ROS.
    node.shutdown()
    rclpy.shutdown()

if __name__ == "__main__":
    main()

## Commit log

2024-02-23 biig progress
    [ee110_alpha_board.csv, ee110_alpha_board.kicad_pcb, ee110_alpha_board.kicad_sch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]
2024-03-18 first revision
    [bill_of_materials.csv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]
2024-04-08 Ilana committing from laptop
    [bill_of_materials.csv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]
2024-04-15 alpha_board about to be sent out
    [bill_of_materials.csv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]
2024-04-15 reorganized folders and started working on 3d print
    [arm-barrel-end-x2.STEP, arm-barrel-end-x2.stl, arm-barrel-x2.STEP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]
2024-04-16 converted all parts to solidworks
    [arm-barrel-end-x2.SLDPRT, arm-barrel-end-x2.STEP, arm-barrel-x2.SLDPRT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]
2024-04-16 reorganized 3d_print folder
    [1_wheel_axle_test.3mf, 2_tread_pin_test.3mf, arm-barrel-end-x2.SLDPRT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]
2024-04-16 finished scaling up all parts by 5/3
    [arm-barrel-end-x2.SLDPRT, arm-barrel-x2.SLDPRT, arm-hinge-axel-x2.SLDPRT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]
2024-04-20 uploaded new files
    [3_tread_teest2.3mf, BracketLock_ESP32_36pin.stl, Bracket_ESP32_36pin.stl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]
2024-04-21 arm assembly
    [arm-barrel-end-x2.SLDPRT, arm-barrel-x2.SLDPRT, arm-hinge-axel-x2.SLDPRT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]
2024-04-21 head assembly, TODO fix file names
    [MG996R.SLDPRT, MG996R.step, MG996R.stl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]
2024-04-21 fixed errors in eyes
    [eye-middle-right_try_mirror.SLDPRT, eye-middle-right_try_mirror_forreal.SLDPRT, head_neck.SLDASM]
2024-04-21 Reorganized folders. Put repository in C/projects/ee110_robot if having issues
    [5_eye_servo-attachment_test.3mf, MG996R.SLDPRT, MG996R.step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]
2024-04-24 flipped head part
    [eye-middle-left.SLDPRT]
2024-04-24 3d print progress
    [10_arm.3mf, 3_tread_test2.3mf, 6_eye_right.3mf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]
2024-04-26 reorganized folders a bit agaiiin, started alpha board revision 2
    [1_standoffs.3mf, BL-Cooler_Box-2.stl, BL-Cooler_Box-3.stl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]
2024-04-27 split body-back, body-top and body-front into smaller parts
    [12_body-back.3mf, 13_body_top.3mf, 14_body_front.3mf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]
2024-04-27 split up into back-copy
    [Body1.SLDPRT, Body10.SLDPRT, Body11.SLDPRT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]
2024-04-28 neck almost done
    [body.SLDASM, neck-bottom-left.SLDPRT, neck-bottom-right.SLDPRT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]
2024-04-28 todo: fixes to neck
    [neck-round-top-left.SLDPRT, neck-round-top-right.SLDPRT, neck-top.SLDPRT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]
2024-05-05 ahh it's a mess
    [16_body_left.3mf, 17_arm_piston_test.3mf, 18_body_front.3mf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]
2024-05-05 neck done??
    [neck-top.SLDPRT, neck.SLDASM]
2024-05-18 much time has passed...
    [20_hand.3mf, 21_just_piston.3mf, 22_neck_parts.3mf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]
2024-10-26 add remaining files
    [30_arms_hinge.3mf, MG996R.SLDPRT, Part4.STEP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]
